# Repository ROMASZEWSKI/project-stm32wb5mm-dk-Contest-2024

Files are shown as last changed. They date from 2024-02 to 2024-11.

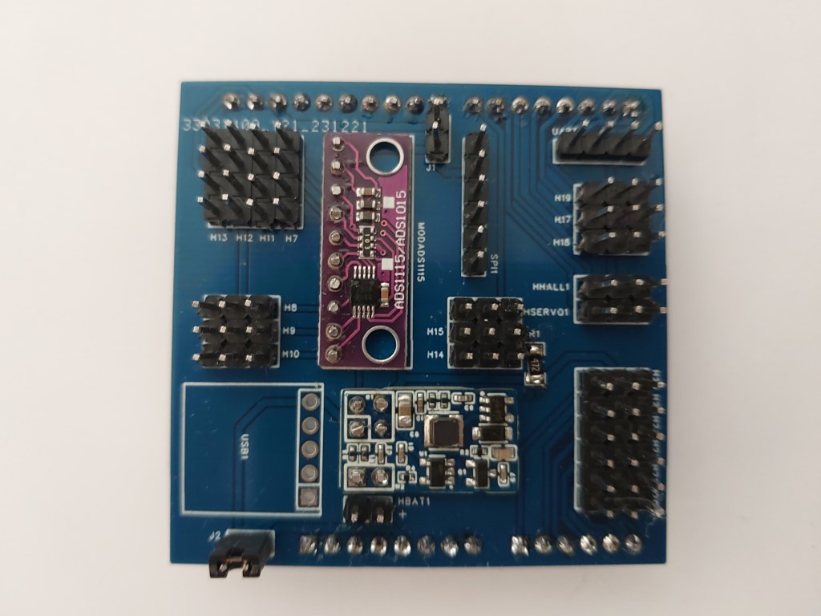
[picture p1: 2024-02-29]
photos/Assembled shield.jpg

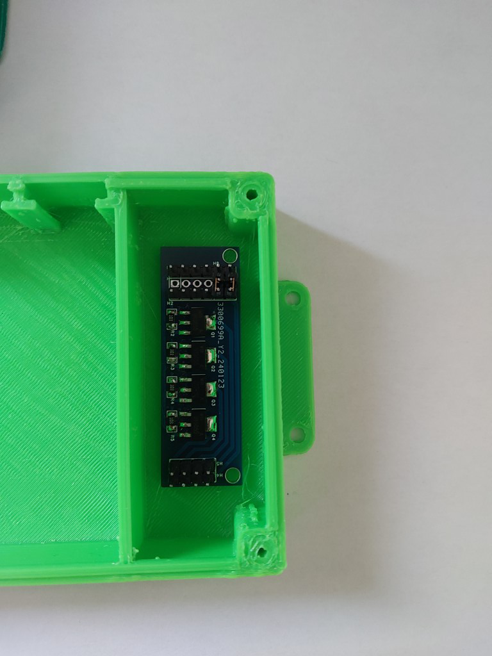
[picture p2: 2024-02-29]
photos/power module installation.jpg

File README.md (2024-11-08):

<h3>Zigbee Environmental measurement center for indoor plants or greenhouse</h3>

The goal of this project is to create with STM32WB5MM-DK a device allowing environmental measurements as well as monitoring of soil humidity and soil temperature of plantations with the management of an automation allowing automated watering and additional illumination according to the measurements.



<h3>Project description</h3>

Sensors in place (Petite)

The goal of this project is to create an environmental measurement unit, lighting and water supply for indoor plants or in a greenhouse using the stm32wb5mm-dk kit with communication in the Zigbee protocol to a server Mqtt linux on the internet through an Mqtt2Zigbee gateway under Windows 11, the information and automations then being processed by the Node-RED application under Linux with web user interface.
The persistence of data is performed by Node-RED to a MariaDB database under Linux.  
A box has been designed and printed on a 3D printer to accommodate the stm32wb5mm-dk card which will be fixed with 3 screws, the main diode is visible through the top case and a window is available to view the Oled display. The two buttons are mechanically transferred to the exterior. The two USB sockets are available and a way is provided for all the wiring. The sensors are fixed on the upper part, each with a receptacle and a window to the outside.

The device must carry out measurements of ambient temperature, ambient humidity, atmospheric pressure (BME280 component), Co2 level, air quality and volatile organic compound or TVOC level. (Ens160 component). An illumination sensor is present to measure the available light. Finally, a capacitive water level sensor is used and fixed to the low level of the water reserve.

Some measurements are taken at each plant using a capacitive sensor and a temperature probe (DS18B20 component). Capacitive sensors are measured with a 16-bit converter (ADS1115 component).

Most sensors can be used via the board's available I2C1 bus. One port is used to create a 1-wire bus for the 3 DS18B20s.

A switching board equipped with power MOSFETs is responsible for relaying the ports of the main board in order to manage 3 watering pumps and a relay for switching a special lamp for plants.

A switching power supply module provides complementary 3v3 power from the 5v source and powers the Shield. This card can also charge a battery and provide 3v3 if  5v is no more present.

The 3 pumps operating from 3v to 5v with brushless motors are immersed in the water reserve and a silicone hose supplies each plant.

In the event of lack of humidity in a plant, the planned automation takes care of supplying water with a given watering time until the desired humidity level is reached.

Phone SMS sending from node-RED is planned when the ambient or plant temperature is too high, when the air quality is too poor or when the water level is too low.

Datas are available and accessible via the Zigbee network, the card behaves as a server and as a router.

Datas are read and refreshed locally every 4s or fixed via an attribute .

The data can be viewed on the Oled display by selecting different screens using buttons 1 and 2.

To force the Zigbee pairing of the card at startup, button 1 must be pressed for 3 seconds.

The available and modifiable data for the lamp and the operating time of the pumps are available to be used by a Zigbee2mqtt coordinator, this coordinator is responsible for retrieving/modifying the information and retransmitting/monitoring topics (path to each data) on a mqtt server.

By using Node-RED specialized in retrieving and modifying Topics, it is possible with a graphical editor to display, storage in dataBase and make some automations.

This project uses different skills: digital electronics, printed circuit design, 3D printing creation, microcontroller programming, internet networks, Mqtt server, Node-RED server, Mariadb database, Linux system.

<h3>My goals are as follows:</h3>

- The first objective which constitutes this project is the commissioning of the stm32wb5mm-dk kit with the use of the sensors on the card and the use of additional sensors connected to a daughter card (two layers shield PCB) . The design of a two specific box printed in ABS or ASA, on 3D printer. The card works in Router/CLUSTER client-server mode. Interface to Zigbee2mqtt application and Node-RED interface.

- The second objective after is the creation of a printed card (4 layers) using the integrated component stm32wb55mmg with its shield (daughter card) and a power supply circuit with battery and solar panel, allowing the exploitation of the low power mode of the component .

Resumption of certain sensors from the first part.

Add water quality TDS sensor. Add high level sensor and automatic supply the water reserve.

- The third objective is to use and evaluate the Thread network in place of Zigbee.

<h3>Ressources links of the project</h3>

<h3>Project description </h3>
https://project.sophe.com/project_description.pdf<br/>
https://github.com/ROMASZEWSKI/project-stm32wb5mm-dk-Contest-2024/blob/main/project_description.pdf<br/>

<h3>All files of the project same as github</h3>
https://project.sophe.com/stm32ContestAllProject.zip
 
<b>For discovering the project :</b>
Read project_description.pdf<br/>
you find stm32cube_project.zip for stm32Cubeproject<br/>
https://github.com/ROMASZEWSKI/project-stm32wb5mm-dk-Contest-2024/blob/main/stm32cube_project.zip<br />
Parse PCB directory<br/>
https://github.com/ROMASZEWSKI/project-stm32wb5mm-dk-Contest-2024/tree/main/PCB<br/>
Parse 3D_print directory<br />
https://github.com/ROMASZEWSKI/project-stm32wb5mm-dk-Contest-2024/tree/main/3D_print<br/>
Parse zigbee2mqtt directory, you can read Zigbee2Mqtt_on_Windows_install.pdf <br />
https://github.com/ROMASZEWSKI/project-stm32wb5mm-dk-Contest-2024/tree/main/zigbee2mqtt<br/>
Parse node-RED directory, you can read Installation_of_node-RED and persistence.pdf <br />
https://github.com/ROMASZEWSKI/project-stm32wb5mm-dk-Contest-2024/tree/main/nodered<br />
And some photos and datasheets.<br />
https://github.com/ROMASZEWSKI/project-stm32wb5mm-dk-Contest-2024/tree/main/photos<br/>
https://github.com/ROMASZEWSKI/project-stm32wb5mm-dk-Contest-2024/blob/main/datasheets.zip<br>
<h3>New version updated with stm32CubeMX support and firmware 1.20 - November 2024</h3>
https://github.com/ROMASZEWSKI/project-stm32wb5mm-dk-Contest-2024/blob/main/greenhouse2.zip<br />

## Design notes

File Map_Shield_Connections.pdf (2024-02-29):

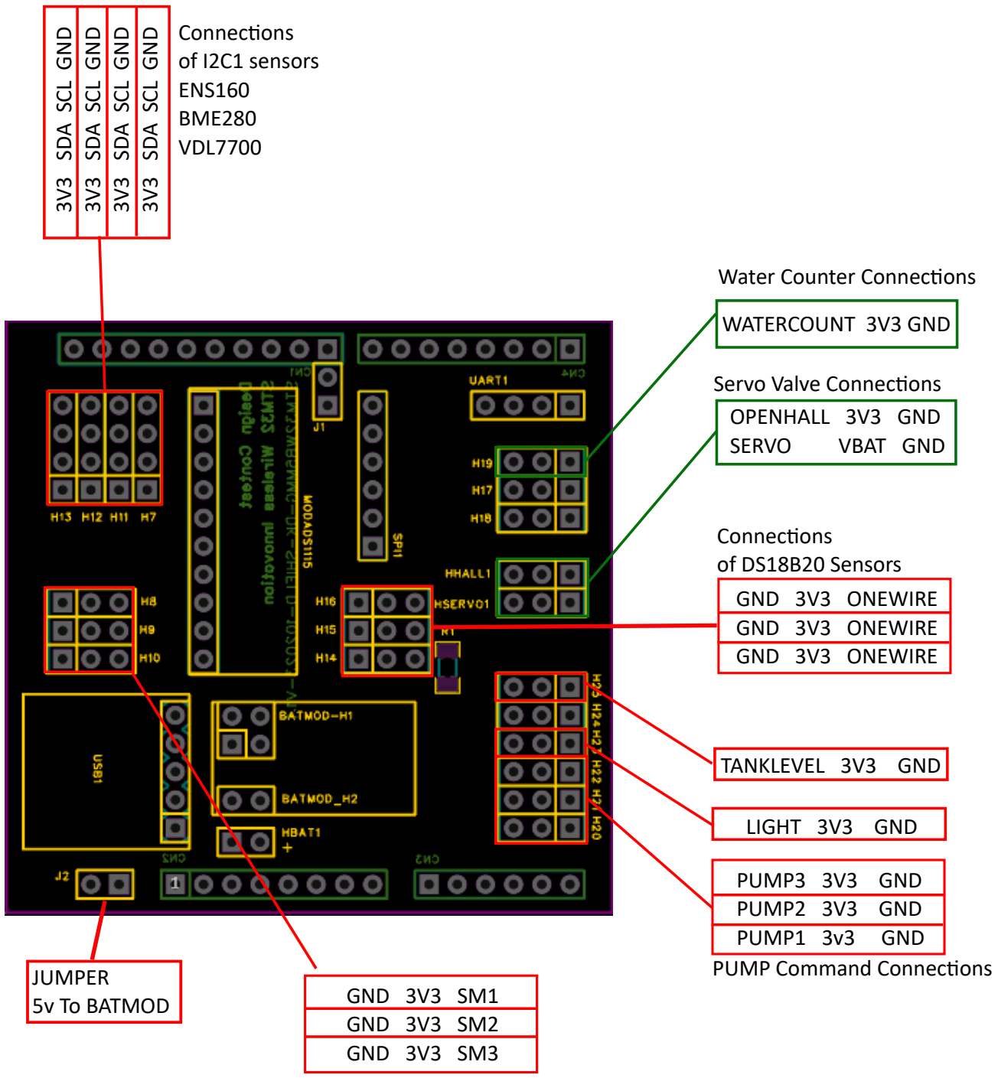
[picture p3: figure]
GND 3V3 ONEWIRE GND 3V3 ONEWIRE GND 3V3 ONEWIRE; JUMPER 5v To BATMOD; Connecons of I2C1 sensors ENS160 BME280 VDL7700; Connecons of DS18B20 Sensors; Water Counter Connecons; Servo Valve Connecons; PUMP Command Connecons; GND 3V3 SM1 GND 3V3 SM2 GND 3V3 SM3; 3V3 SDA SCL GND; PUMP3 3V3 GND PUMP2 3V3 GND PUMP1 3v3 GND; OPENHALL 3V3 GND; SERVO; VBAT GND; WATERCOUNT 3V3 GND; LIGHT 3V3 GND; TANKLEVEL 3V3 GND

Connecons
of Soil Moisture Sensors

Current project

## SHIELD CARD FOR STM32WB5MM-DK MODULE

Extended project

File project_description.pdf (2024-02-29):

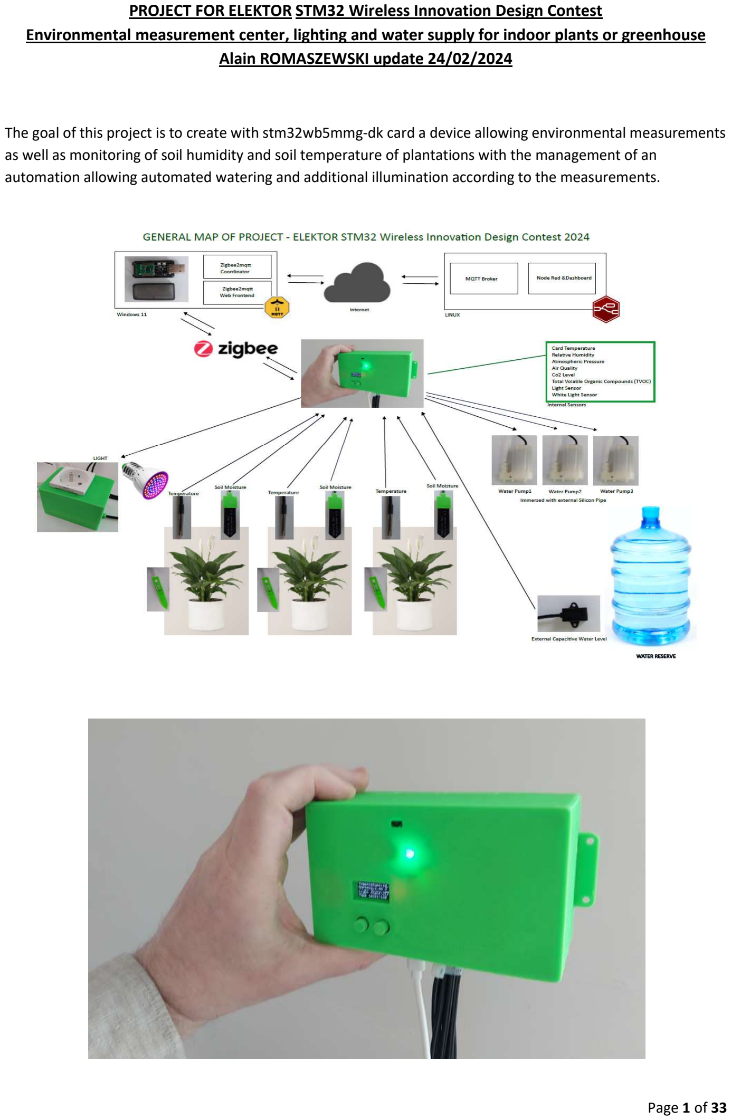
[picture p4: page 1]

Page 1 of 33

PROJECT FOR ELEKTOR STM32 Wireless Innovation Design Contest Environmental measurement center, lighting and water supply for indoor plants or greenhouse Alain ROMASZEWSKI update 24/02/2024

The goal of this project is to create with stm32wb5mmg-dk card a device allowing environmental measurements as well as monitoring of soil humidity and soil temperature of plantations with the management of an automation allowing automated watering and additional illumination according to the measurements.

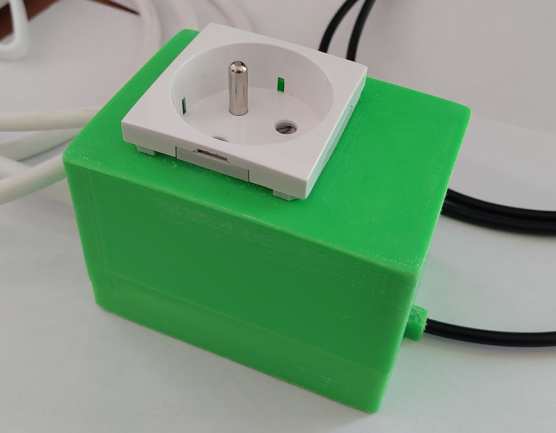
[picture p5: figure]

Page 2 of 33

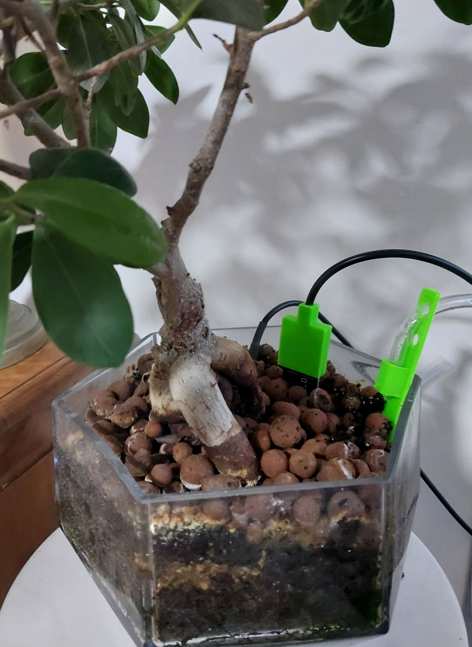
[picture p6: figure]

Project description

The objective of this project is to create an environmental measurement unit, lighting and water supply for indoor plants or in a greenhouse using the stm32wb5mm-dk kit with communication in the Zigbee protocol to a server Mqtt linux on the internet through an Mqtt2Zigbee gateway under Windows 11, the information and automations then being processed by the Node-RED application under Linux with web user interface.
The persistence of data is performed by Node-RED to a MariaDB database under Linux.

A box has been designed and printed on a 3D printer to accommodate the stm32wb5mm-dk card which will be fixed with 3 screws, the main diode is visible through the top case and a window is available to view the Oled display. The two buttons are mechanically transferred to the exterior. The two USB sockets are available and a way is provided for all the wiring. The sensors are fixed on the upper part, each with a receptacle and a window to the outside.

The device must carry out measurements of ambient temperature, ambient humidity, atmospheric pressure (BME280 component), Co2 level, air quality and volatile organic compound or TVOC level. (Ens160 component). An illumination sensor is present to measure the available light. Finally, a capacitive water level sensor is used and fixed to the low level of the water reserve.

Some measurements are taken at each plant using a capacitive sensor and a temperature probe (DS18B20 component). Capacitive sensors are measured with a 16-bit converter (ADS1115 component).

Most sensors can be used via the board's available I2C1 bus. One port is used to create a 1-wire bus for the 3 DS18B20s.

A switching board equipped with power MOSFETs is responsible for relaying the ports of the main board in order to manage 3 watering pumps and an external static relay for switching a special lamp for plants.

Page 3 of 33

A switching power supply module provides complementary 3v3 power from the 5v source and powers the Shield. This card can also charge a battery and provide 3v3 if 5v is no more present.

The 3 pumps operating from 3v to 5v with brushless motors are immersed in the water reserve and a silicone hose supplies each plant.

In the event of lack of humidity in a plant, the planned automation takes care of supplying water with a given watering time until the desired humidity level is reached.

Phone SMS sending from node-RED is planned when the ambient or plant temperature is too high, when the air quality is too poor or when the water level is too low.

Datas are available and accessible via the Zigbee network, the card behaves as a server and as a router.

Datas are read and refreshed locally every 500ms.

The data can be viewed on the Oled display by selecting different screens using buttons 1 and 2.

To force the Zigbee pairing of the card at startup, button 1 must be pressed for 3 seconds.

The available and modifiable data for the lamp and the operating time of the pumps are available to be used by a Zigbee2mqtt coordinator, this coordinator is responsible for retrieving/modifying the information and retransmitting/monitoring topics (path to each data) on a mqtt server.

By using Node-RED specialized in retrieving and modifying Topics, it is possible with a graphical editor to display, storage in dataBase and make some automations.

This project uses different skills: digital electronics, printed circuit design, 3D printing creation, microcontroller programming, internet networks, Mqtt server, Node-RED server, Mariadb database, Linux system.

My objectives are as follows:

- The first objective which constitutes this project is the commissioning of the stm32wb5mm-dk kit with the use of the sensors on the card and the use of additional sensors connected to a daughter card (shield) made on both sides. The design of a specific box printed in ABS or ASA, on a 3D printer. The card works in Router/CLUSTER client-server mode. Interface to Zigbee2mqtt, Node-RED interface.
- The second objective is the creation of a printed card (4 layers) using the integrated component
stm32wb55mmg with its shield (daughter card) and a power supply circuit with battery and solar panel, allowing the exploitation of the low power mode of the component .

Resumption of certain sensors from the first part.

Add water quality TDS sensor. Add high level sensor and automatic supply of the water reserve.

- The third objective is to use and evaluate the Thread network in place of Zigbee.

Project Hardware

Motherboard: stm32wb5mm-dk.

Page 4 of 33

This card consists of an integrated stm32wb55mmg component equipped with an M4 processor for processing and an M0+ coprocessor for BLUETOOTH, Zigbee and Thread communications.

We will deal here with Zigbee 3.0 mode. The card includes a OLED display of 128x64 pixels, 1 RGB diode, 2 push buttons, 1 sensitive key, 1 temperature sensor, 1 Gyroscopic and velocity sensor, 1 distance sensor, movements and a microphone.

The display is connected to the SPI interface and the sensors to the I2C3 bus. The card exposes different ports, an I2C1 bus, a Low Power UART and SPI bus among others.

Modules and sensors already present and used on the main card:

An OLED display for messages and displays.
A diode for signaling measurements taken.
First button to associate the server with the Zigbee coordinator when booting the system.
An STS22H temperature sensor integrated into the card (allowing you to know the temperature of the case and the card)
A gyroscope and velocity sensor (not necessarily useful here but exposed if necessary)
Two buttons used to scroll through the different displays. The same button can be used when booting the card to associate it with the Zigbee network.

Modules and sensors present on Shield card with Arduino type connectors:

A 16-bit (4-channel) ADS1115 type converter module. Allowing the measurement of battery voltage, the measurement of 3 soil humidity sensors.

Page 5 of 33

A BME280 type temperature, humidity and atmospheric pressure measurement module.

An ENS160 pollution and air quality measurement module, QA, Tvoc, Co2 measurement associated with an Aht25 sensor measuring temperature and hygrometry for the calibration of the ENS160 module.

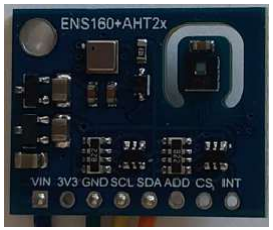
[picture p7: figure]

A VEML7700 type brightness measurement module.

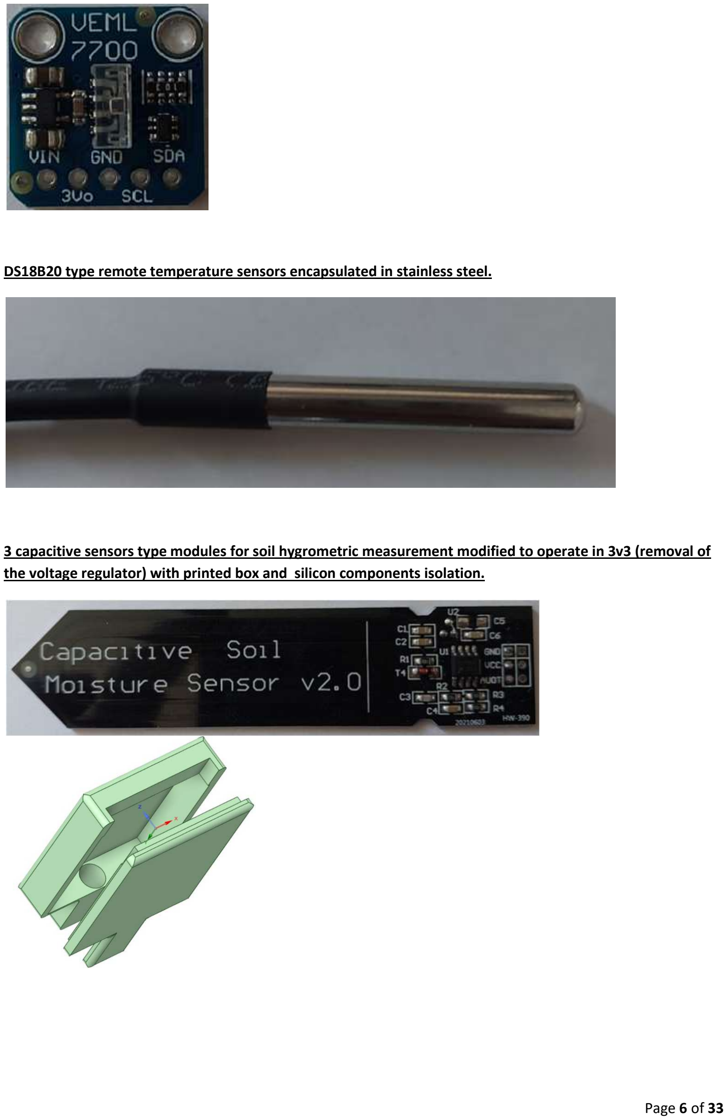
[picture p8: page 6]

DS18B20 type remote temperature sensors encapsulate

### 3 capacitive sensors type modules for soil hygrometric measurement modif

the voltage regulator) with printed box and

d in stainless steel.

type modules for soil hygrometric measurement modified to operate in 3v3 (removal of silicon components isolation.

Page 6 of 33

ied to operate in 3v3 (removal of

A power control module for activating 3 watering pumps. Eit activating Relay for Light.

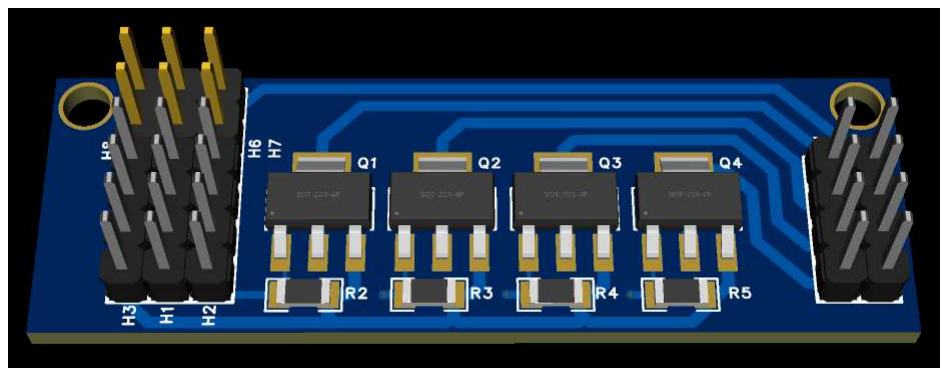
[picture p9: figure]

External box with Static Relay

her from 3v3/5v immersed

Page 7 of 33

brushless pumps and

Page 8 of 33

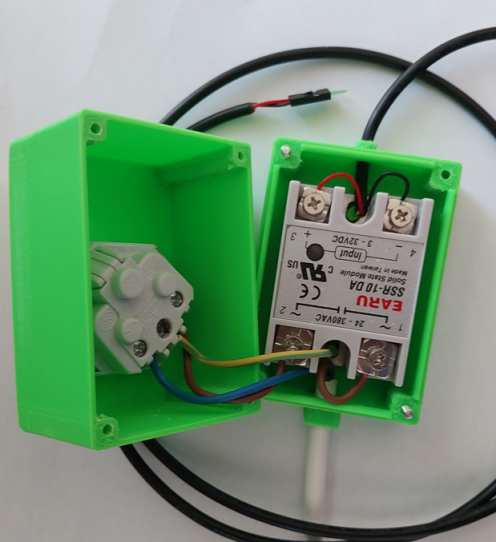
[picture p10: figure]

Schematic of connections in file joined.

Guide for pipe and pomp

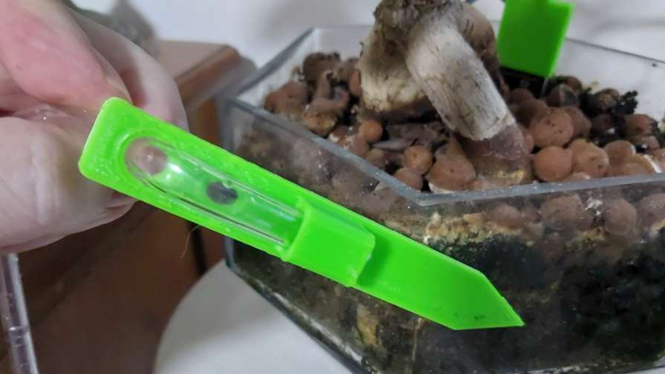
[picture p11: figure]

A capacitive module 3v3 detector for checking the low level of the water reserve.

Page 9 of 33

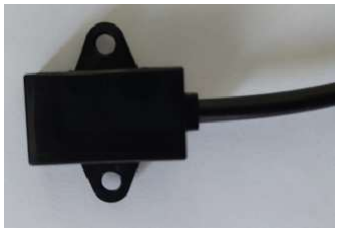
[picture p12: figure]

you need to attach the sensor using a double-sided adhesive to the lowest level of the tank.

A switching charging and power supply module to manage the charging of an 18650 battery used for pumps power and to provide up to 1A at 3.4 volts for the shield here, the input voltage is 5 volts

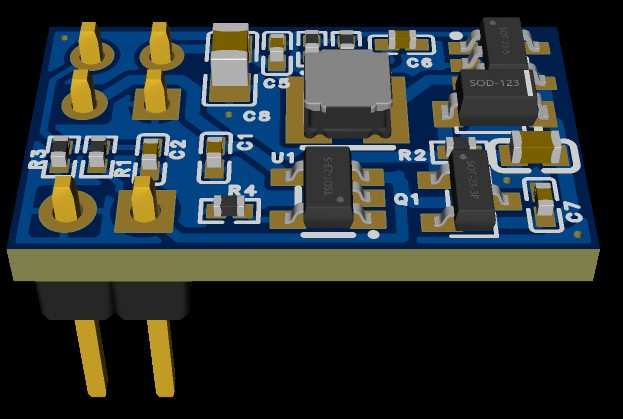
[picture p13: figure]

A shield card connected to the Arduino connectors on the stm32wb5mm-dk board.

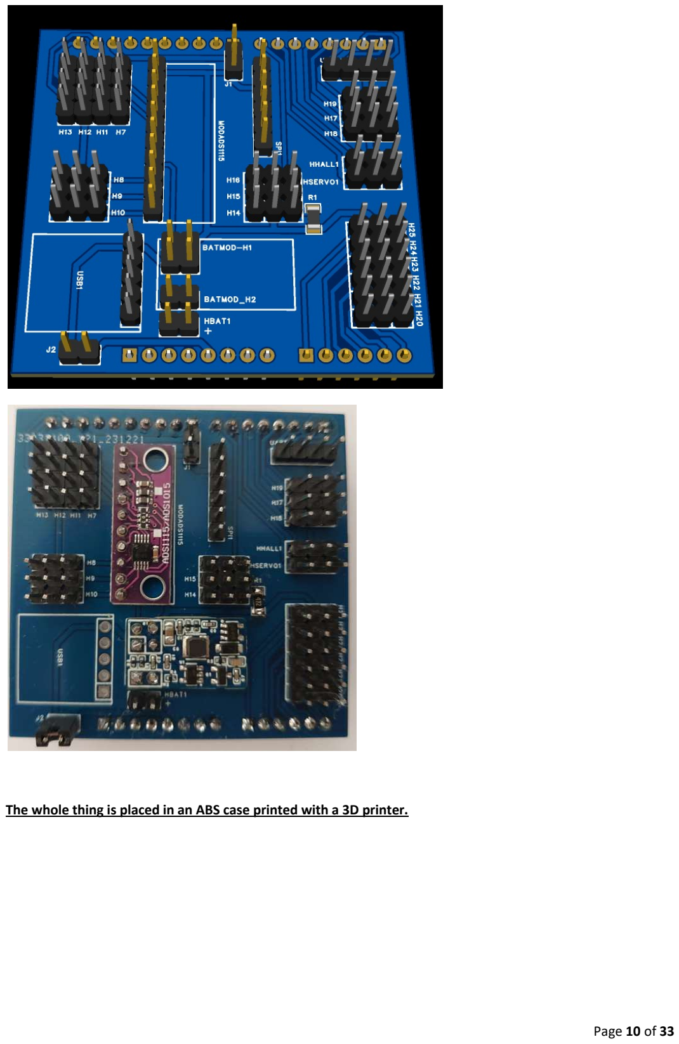
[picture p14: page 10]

Page 10 of 33

The whole thing is placed in an ABS case printed with a 3D printer.

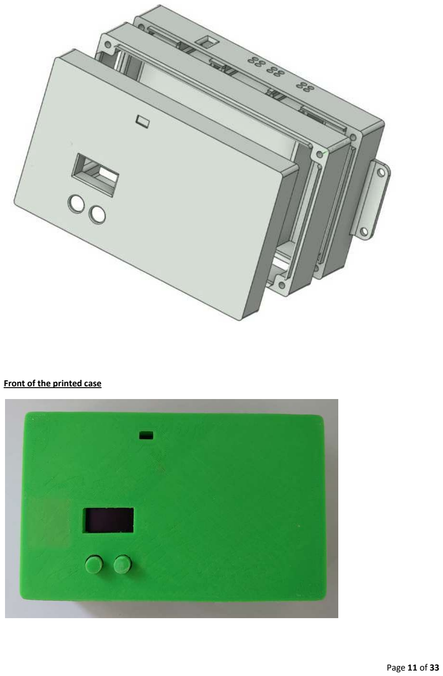
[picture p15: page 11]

Page 11 of 33

Front of the printed case

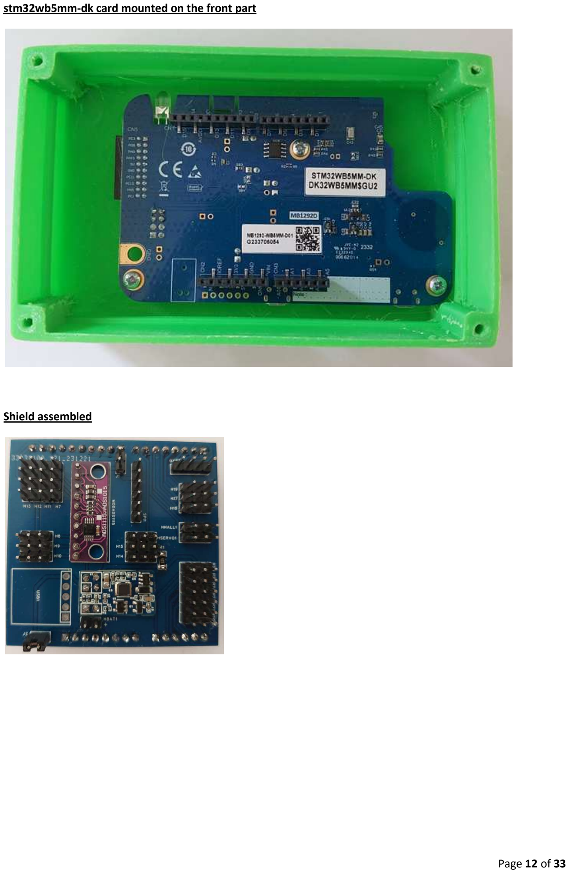
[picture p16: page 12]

Page 12 of 33

stm32wb5mm-dk card mounted on the front part

Shield assembled

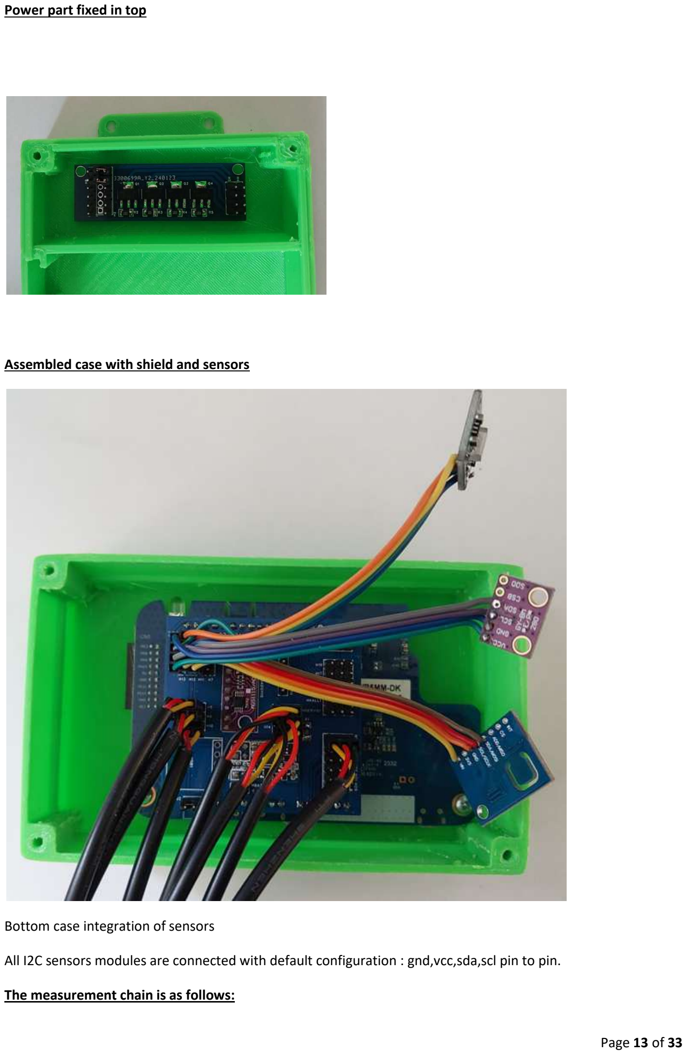
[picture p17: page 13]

Page 13 of 33

Power part fixed in top

Assembled case with shield and sensors

Bottom case integration of sensors

All I2C sensors modules are connected with default configuration : gnd,vcc,sda,scl pin to pin.

The measurement chain is as follows:

Page 14 of 33

The stm32wb5mmg-dk module and its daughter card exhibit regular measurements as a Zigbee server/router.

The zigbee2mqtt gateway client installed on a Windows 11 machine with a compatible Zigbee USB key is responsible for powering an MQTT event server installed on a remote server via the Internet. The gateway informs about the state of the network and the state of the attributes of the modules that have been associated with this gateway.

The results requested from the sensors are organized in a tree of Topics (access paths) on the MQTT server. MQTT GET requests are used to query the clusters of measurement results present on the remote Zigbee server.

It is also possible to transmit MQTT requests to modify a state or a value commanding an action to the Zigbee Remote client in order to activate, for example, a pump or a valve for a period of time.

Finally, the Node-RED application allows you to manage MQTT events and launch attribute readings from Clusters and launch actions via Mqtt set requests.

In passing, the events are stored in a MARIADB database to ensure the persistence of information and statistical processing of events.

Quick summary of the architecture of a Zigbee Network

The Zigbee protocol works using a mesh architecture and follows a communication model based on the master-slave principle. Here is an explanation of how the Zigbee protocol works:

Mesh Topology : Zigbee uses a mesh network topology, which means that each node (device or device) can communicate directly with other nodes nearby. Each node can act as a transmitter, a receiver and optionally a router.

Zigbee Nodes : There are three main types of Zigbee nodes:

1. Network coordinator (Zigbee Coordinator) : It is the main node which initializes and organizes the formation of the network.
2. Network router (Zigbee Router) : This node participates in the routing of information in order to facilitate its delivery. It can participate in the Zigbee network as End Nodes.
3. Zigbee End Devices : These are simple devices that join the Zigbee network. They are usually battery powered and are designed to minimize their power consumption.

Network Formation : When setting up a Zigbee network, the coordinator first emits a signal inviting other devices to join the network. Interested end nodes communicate with the coordinator to join the network. Once associated, endpoints can transmit data to this coordinator.

Master-Slave Communication: Zigbee uses a master-slave model, where the coordinator acts as the master of the network, and the end nodes are the slaves. End nodes can serve data to the coordinator, they cannot communicate directly with each other in most cases. However, using mesh topology, data can be routed through other nodes in the network to reach its destination with router node.

Security : Zigbee incorporates security mechanisms such as data encryption and device authentication.

Energy management : Zigbee is designed to be energy efficient, especially for battery-powered endpoints. Devices can go into sleep mode to save power and can be woken up when communication is needed.

Quick summary about the Zigbee protocol:

Page 15 of 33

Zigbee is based on the 802.15.4 physical protocol sharing the 2.4Ghertz WiFi frequency band. The band is divided into 16 channels (11 to 26), some channels are vacant and can be more particularly used in our case (15, 20, 25 for example). Of course all devices connected to the main coordinator must use the same channel as this one.

Each Router or Endpoint must first contact its coordinator in order to establish an exchange of keys and create a secure connection (or association). This session/association must be memorized between the Router/Endpoint and the coordinator.

This operation must be done once the network is installed, the coordinator authorizing this association only over a short period of time, each device having a unique 64-bit MAC address, the coordinator is also able to select and secure the association.

During the association, the coordinator retrieves a unique 64-bit address, allowing the Zigbee Node to be identified.

The Zigbee Node is divided into 1 or more EndPoints (between 1 and 240).

Each Endpoint has one or more Clusters representing a function standardized by the Zigbee or proprietary protocol with default attributes depending on the functions.

For each Cluster, it is therefore necessary to define its main function, its default and/or complementary attributes which can then be translated into a set of values or actions initiated by the coordinator.

Each attribute has a standardized 16-bit identifier, a value with a type (8, 16, 32, 64 bits, strings, enumeration, table, etc.). It can be read, written and/or reported on the network periodically or even persistent (its value is then memorized by the EndPoint). For Alarm or command mode the attribute can be transmitted to the coordinator as soon as the event occurs.

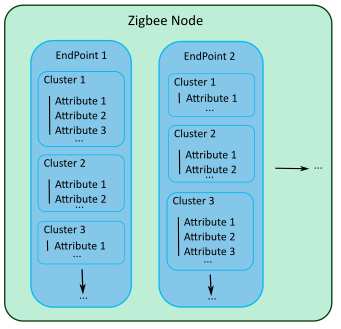
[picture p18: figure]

In our case of physical measurements to be taken, we will work as a query server on the attributes, the client coordinator being responsible for regularly querying the attributes in order to retrieve and store the information.

To carry out actions, the coordinator can modify attribute values on the EndPoint, the latter upon receipt will execute the requested tasks, indicating its state by modifying attributes.

Page 16 of 33

At the development level, ST Microelectronics has released a pre-compiled library for Cluster management. This is also accompanied by a Microcode intended for the M0+ communication coprocessor, depending on the final need and the desired protocol.

It is possible to add attributes to an existing Cluster depending on the desired final application.

Microcontroller Software Development Tool

For development, we will use the STM32CubeIDE v1.14.0 tool in C language, based on an existing Zigbee example.

It was necessary to rewrite drivers in C language available in the Arduino universe.

The existing example uses a non-preemptive pseudo system provided as an example by the manufacturer allowing the Zigbee network layer to be managed and tasks to be carried out sequentially by priority. https://www.st.com/en/development-tools/stm32cubeide.html

Zigbee2mqtt Gateway

This Open Source gateway works with the Node.js framework and is therefore programmed in Javascript. It can be installed under Linux or Windows environment.
It has a Web interface allowing you to manage the nodes and a configuration file allowing you to configure the gateway and recognize new nodes.

It can manage different Zigbee USB adapters on the market, here we will use a Zigbee 3.0 USB Dongle adapter based on Silicon Labs EFR32MG21 with pre-flashed EZSP V8.0.

It is responsible for transmitting the state of the gateway, the state of the nodes and the value of the node attributes to different Topics of an Mqtt server.

https://github.com/ROMASZEWSKI/zigbee2mqtt

https://github.com/ROMASZEWSKI/zigbee2mqtt-frontend

Managing MQTT data with Node-RED

This open source application works with the Node .js framework and is therefore programmed in Javascript. It can be installed under Linux or Windows environment.

It has a Web interface and allows you to process information flows from Mqtt servers, to work with databases (here MariaDB) and finally to generate events with scripts and graphic flows.

https://github.com/node-red/node-red

https://nodered.org/

Page 17 of 33

3D design

3D design is carried out by the free DesignSpark Mechanical 6 software (free version of SpaceClaim).

https://fr.rs-online.com/web/generalDisplay.html?id=designspark/designspark-mechanical

https://www.ansys.com/products/3d-design/ansys-spaceclaim

3D FDM printing

Printing is done with PrusaSlicer 2.6 software on an upgraded ANET ET 4 PRO.

The creations use either ABS filament or ASA filament (UV resistant).

https://www.prusa3d.com/en/page/prusaslicer_424/

https://anet3d.com/pages/et4

Printed Circuit Board Design

The design uses EasyEDA PRO v2.1.42 software and the ultra-fast, low-cost production line that goes with it.

https://easyeda.com/

Design and description of the functions of the shield card with Arduino connectors

This card has a soldered ADS1115 module (Fig.2) and a complementary soldered 5v -> 3.3v 1A switching power supply module with the possibility of battery charging so as not to overuse the power supply of the main map. The battery is not really useful at the moment but useful in subsequent projects.

It includes all the 2.54mm Dupont Male connectors for the various sensors.

Description of the main application

Installing or upgrade First the Firmware for M0+ Co-processor

the STM32WB5x processor works with an M0 co-processor which uses firmware provided by ST. This firmware is available in the STM32CubeWB PACK available here:

the stm32WB5x processor works with an M0 co-processor which uses firmware provided by ST. This firmware is available in the STM32CubeWB PACK available here:

https://github.com/STMicroelectronics/STM32CubeWB/tree/master/Projects/STM32WB_Copro_Wireless_Binaries/STM32WB5x

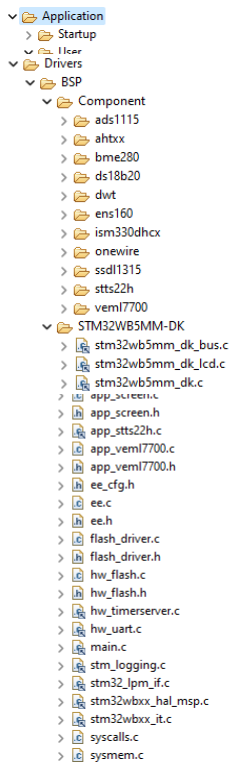
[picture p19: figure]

Page 18 of 33

We will use the stm32wb5x_Zigbee_FFD_fw.bin file in its revision 1.18.

Programming of the coprocessor is carried out via the FUS interface accessible via the STM32CubeProgrammer software.

Firmware file : stm32wb5x_Zigbee_FFD_fw.bin

Start Address : 0x080A0000

Description of the Drivers

In this directory we find the .c and .h drivers for the different sensors used:

ads1115: 16-bit AD Converter Driver.
ahtxx: Temperature and humidity sensor driver for calibration of the ENS160 bme280: Temperature, relative humidity and atmospheric pressure sensor driver.
ds18b20: Driver for 1-wire temperature sensors.
dwt: microsecond delay generator driver for onewire.
ens160: CO2, QA and Tvoc sensor driver. ism330dhcx: onewire gyroscope driver :
1-wire sensor driver
ssdl1315: Oled display driver
sts22h: temperature sensor driver of the
veml7700 card: light sensor driver.
The STM32WB5MM-DK directory which includes the button, RGB LED and Oled display drivers.

Application modules

app_ads1115: High level control of AD converter.

app_ahtxx: High level control of the temperature/humidity sensor of the ENS160
app_automat: Control of automations: Pumps, Light, level.

Page 19 of 33

app_bme280: High level control of the bme280 temperature/humidity/pressure sensor. app_clusters: definitions and activation of Zigbee clusters.

app_ds18b20: High level control of DS18B20 1-wire temperature sensors.
app_ens160: High level control of the pollution sensor: Co2, QA, TVoc.
app_entry: Groups the Zigbee protocol initialization subroutines.
app_ScheduleMeasure: Management of cyclical measurements and updating of Zigbee attributes and management of automations. Display of measurements by APP_DBG. MAIN PROGRAM
app_screen: Management of screens displaying the measurement results with selection by button 1 and 2 to scroll.
app_sts22h: High level control of the board temperature sensor.
app_veml7700: High level control of the light sensor.

ee, flash_driver,hw_flash: Set of subroutines used to emulate an eeprom on a Flash memory area of the processor. Used to save Zigbee connection information.
hw_timerserver: Management of timers for delays and the sequencer.

hw_uart: Serial interface management for APP_DBG displays.

main: Management of basic processor initialization.

stm_logging: management of debug displays to the serial link.

app_zigbee: this module configures the Zigbee layer, different calls are made to the modules described previously.

The application is based on the STM32_WPAN Middlewares library allowing the use of Zigbee communication.

Finally, the Utilities directory containing high-level management of the Oled display as well as sequencer for the management and synchronization of non-preemptive tasks.

Page 20 of 33

How the application works

The application configures on channel 15 Zigbee, an EndPoint 1 server, and a Temperature Measurement type cluster, proprietary attributes are then added to this standardized cluster. This choice was made after trying to create proprietary Cluster but after some trouble with the pre-compiled zcl library, on the other hand the application is stable and simple.

Cyclically, all sensors are interrogated and the results placed in each corresponding attribute of the Cluster, the delay is 20 seconds by default, but can be modified with a cluster attribute (ATTREFRESHMEAS).

The board's temperature sensor is used via the I2C3 interface.
The ADS1115, ENS160, BME280, VEML7700 and AHT25 sensors are used via the I2C1 interface. The soil humidity sensors have been modified to work at 3.3v and are connected to 3 inputs of the ADS1115 A/D converter. The first converter measures the Battery charging voltage.

The 3 DS18B20 1-wire bus type temperature sensors are connected to 1 PORT bit.
The Capacitive water tank level sensor is connected to 1 PORT bit.

The AHT25 temperature/humidity sensor supplied with the ENS160 must be interrogated less often because it tends to heat up, which is a shame for the measurement!

The activation of the pumps is managed by an activation time set in ms by their PlantWaterAlimentationX attribute (where X value is 1,2 or 3).

If this attribute is different from 0, the pump is started and the attribute is decremented by time to 0 and the pump is stopped. Each pump is on 1 PORT bit. The ON/OFF pump status is reported on a Cluster attribute PlantWaterAlimentationStateX.

If the Light attribute is 1 the light is on. 1 port bit. With the attribute PlantLight.

List of attributes

The app_clusters.h file lists the attributes used, each attribute has a 16-bit identifier.

Page 21 of 33

The app_clusters.c file declares the list of attributes to add to the Cluster.

Each attribute must be declared with its type, its minimum and maximum value, as well as its cyclical reportability or modification to the network.

The temperature in °C * 100 is a signed 16-bit integer.
The atmospheric pressure in hPa *10 is an unsigned 16-bit integer, not corrected with the altitude value. The relative humidity and soil humidity in % *10 is an unsigned 16-bit integer.
The battery voltage in mV is an unsigned 16-bit integer. The Co2 in ppm is an unsigned 16-bit integer. The Tvoc in pbm is an unsigned 16-bit integer.
The values in ohms of resistors R1, R2, R3 and R4 for gas detection are unsigned 32-bit integers.
The air quality is an unsigned 8-bit integer.
The motor and light on/off control is an unsigned 8-bit integer.
The water supply control is an unsigned 16-bit integer representing the time in ms.
The on/off pump state On/Off is an unsigned 8-bit integer.
The air quality sensor is an unsigned 8-bit integer.
The on/off tank level is an unsigned 8-bit integer.
The identifier DS18B20 is an unsigned 64-bit integer.

In order not to consume too much current on the card ports, a control module comprising 4 N-channel power MOSFETs makes it possible to control the pump motors and a relay for the lamp.

The app_automat.c file manages the automation and actions of the pumps, the lamp and the level sensor.

The app_SheduleMeasure.c file cyclically retrieves the value of the sensors by placing them in the Cluster attributes, a display is reported on the serial link.

The app_screen.c file manages the display of information screens, the different screens can be selected using the two buttons on the card for cyclical selection.

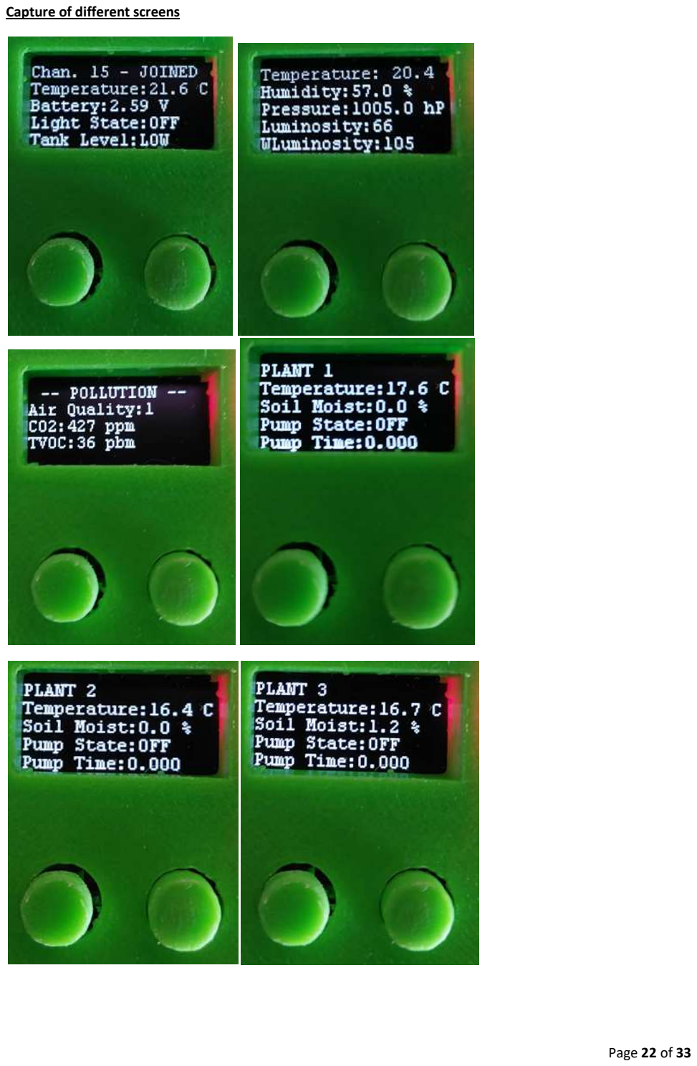
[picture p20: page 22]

Page 22 of 33

Capture of different screens

Page 23 of 33

Page 24 of 33

Installation and configuration of the Zigbee2Mqtt application

The Zigbee coordinator will be the Zigbee2Mqtt application installed on Windows 11 with a Zigbee 3.0 USB adapter based on Silicon Labs EFR32MG21 with EZSP v8.

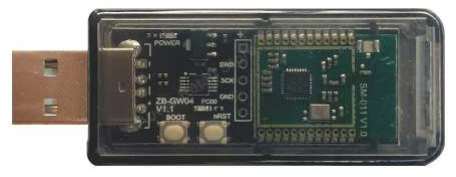
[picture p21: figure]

This application written in JavaScript with the Node.js framework will offer management of the coordinator via a Web interface and allow you to configure and transmit the state of each attribute of the Cluster to a Topic Set or Get of the remote Mqtt server. So by subscribing to an Mqtt Topic it is possible either to retrieve the value of the attribute or to modify it.

It will be necessary to modify the definition of Clusters in order to be able to correctly visualize the attributes.

You can discover this part in other documents and files join in zigbeetomqtt zip.

Installing an MQTT server

It is the MOSQUITTO application which will be used to manage an Mqtt server and will be installed on a Debian 12 VPS from OVH with ispconfig auto installation.

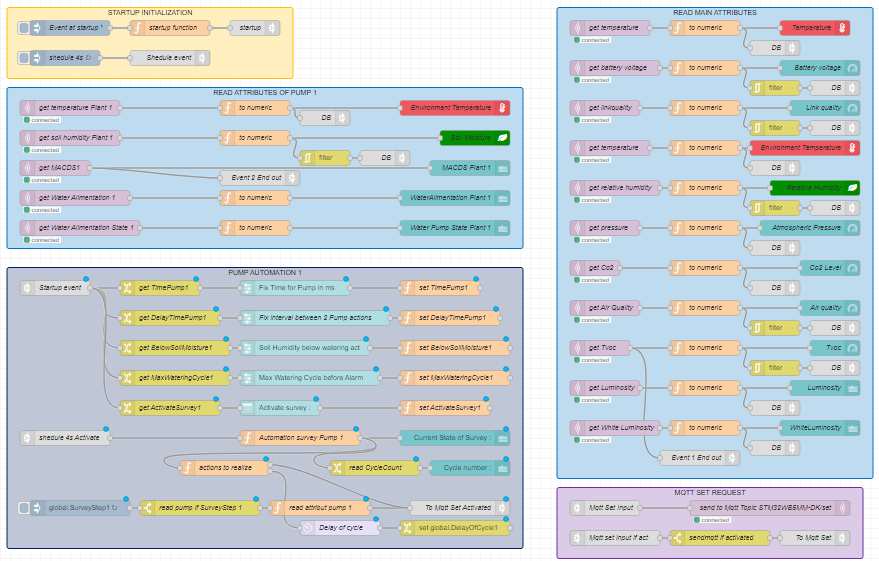
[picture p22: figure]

Page 25 of 33

Installation and configuration of the Node-RED application

This application written in Javascript and Node.js Framework allows you to connect to the Mqtt server and manage the storage of attributes in a database, as well as to carry out automation and alert management actions. It will be installed on a Debian 12 VPS.

This application has a web interface to graphically manage and schedule events. Another dashbord graphical interface allows you to view information and take action via widgets.

Node-RED have the capacity to request mqtt server and act with Mariadb database.

The flows of the project manage a light automation :

- Manual Light ON/OFF
- ON/OFF if brightness is too low.
- Sheduler with multiple times by week.
- Sheduler + brightness is too low.
- Solar Day/night + On if brightness is too low.

The flows of the project manage Pump automation :

- If the level of soil moisture is too low, it is possible to activate a cycle of watering with some limits and if

the water tank level is hight.(pumping delay and wait delay with a number of maximum cycle).

Screens of flows used :

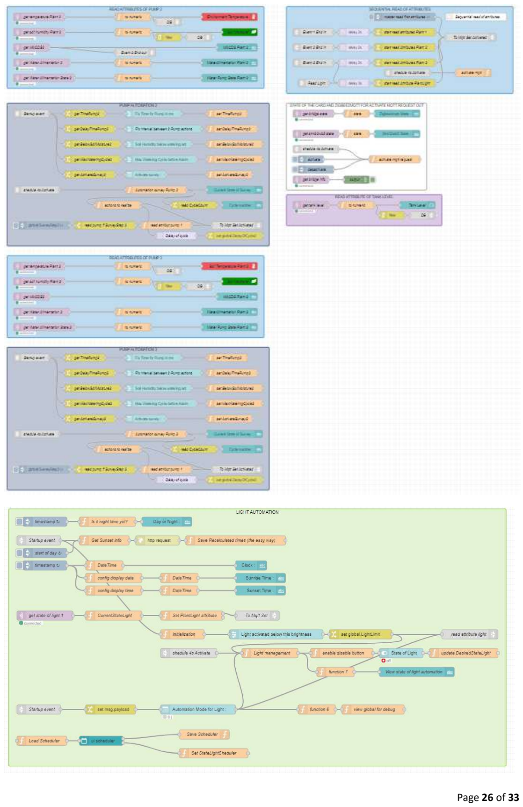
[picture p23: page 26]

Page 26 of 33

Page 27 of 33

All flows and detailed explanations are joined with this project in nodered directory.

NodeRed Dashboard sample screens

Page 28 of 33

Page 29 of 33

RESSOURCES LINKS OF THIS PROJECT

https://project.sophe.com/stm32ContestAllProject.zip

Page 30 of 33

Somes other details of my second goal in low power mode

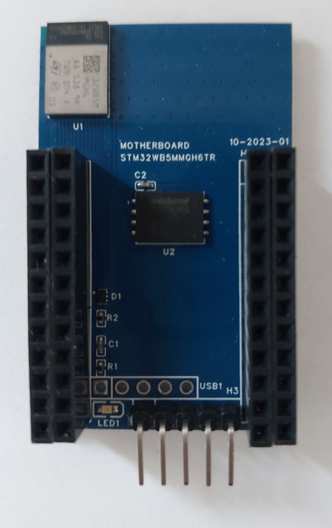
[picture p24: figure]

Creation of light motherboard (4 layers) with stm32wb5mmgh6tr and flash 32M for recording measure.

Very difficult to produce…

PCB attached to this project.

Programming with stm32programmer

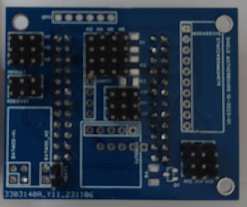
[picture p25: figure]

Shield for low power usage (2 layers)

PCB attached to this project

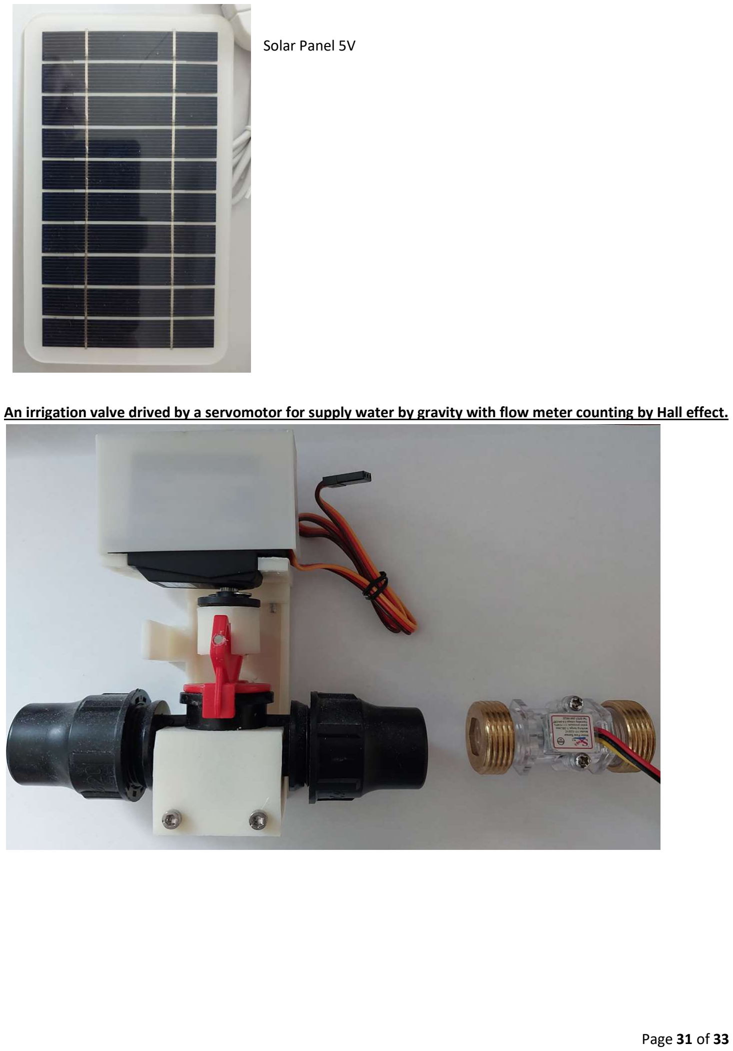
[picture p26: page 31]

Page 31 of 33

Solar Panel 5V

An irrigation valve drived by a servomotor for supply water by gravity with flow meter counting by Hall effect.


TDS Sensor for testing quality water

Integrate Zigbee2mqtt Coordinator and Mosquitto in

connected on ADS1115.

Page 32 of 33

Page 33 of 33

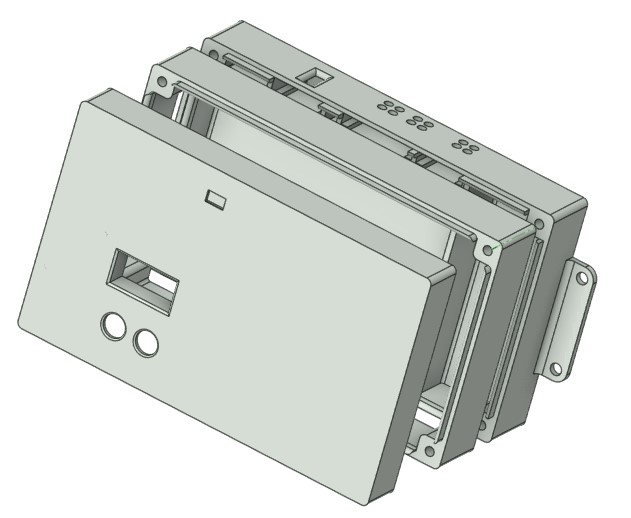
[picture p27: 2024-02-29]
photos/3D_design_from_top.jpg

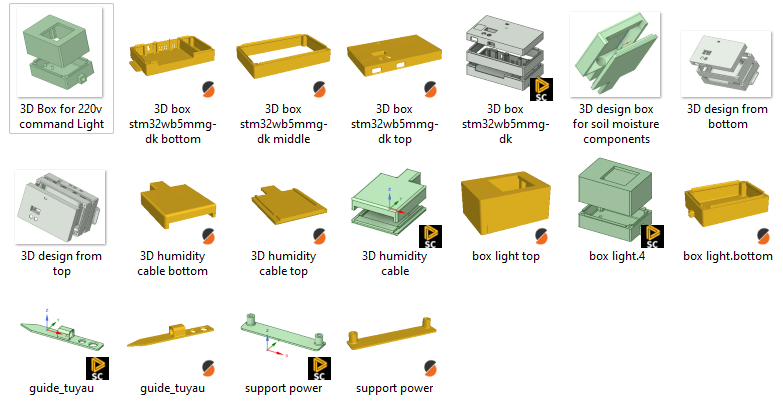
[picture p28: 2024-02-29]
photos/3D overview of models.png

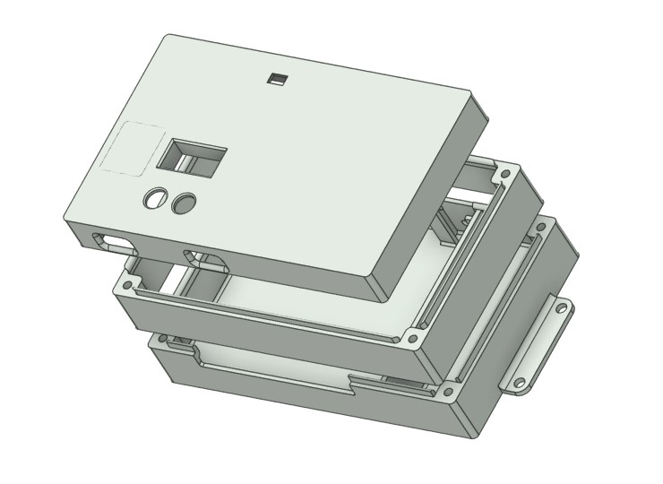
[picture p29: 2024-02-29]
3D_print/3D design from bottom.jpg

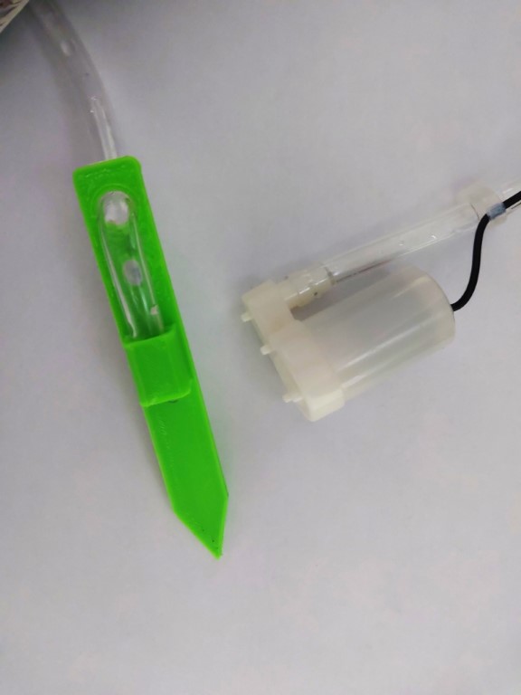
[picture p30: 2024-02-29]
photos/motor and pipe.jpg

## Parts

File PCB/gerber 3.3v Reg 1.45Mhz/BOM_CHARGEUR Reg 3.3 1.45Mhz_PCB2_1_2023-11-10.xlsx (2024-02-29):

No. | Quantity | Comment | Designator | Footprint | Value | Manufacturer Part | Manufacturer | Supplier Part | Supplier
1 | 1 | 1uF | C1 | C0402 | 1uF |  |  | C1525
2 | 3 | 100nF | C2,C5,C7 | C0402 | 100nF |  |  | C1525
3 | 1 | 10uF | C3 | C0603 | 10uF
4 | 1 | 8.2pF | C6 | C0402 | 8.2pF
5 | 1 | 10uF | C8 | C0805 | 10uF
6 | 1 | 1N5819W | D1 | SOD-123_L2.7-W1.6-LS3.7-RD |  | 1N5819W | Hottech(合科泰) | C2988774 | LCSC
7 | 1 | 2.2uH | L1 | IND-SMD_L3.0-W3.0 | 2.2uH | SWPA3015S2R2MT | Sunlord(顺络) | C43389 | LCSC
8 | 1 | CJ2301 | Q1 | SOT-23-3_L2.9-W1.3-P1.90-LS2.4-BR |  | CJ2301 | CJ(江苏长电/长晶) | C2910170 | LCSC
9 | 3 | 100K | R1,R2,R3 | R0402 | 100K
10 | 1 | 2K | R4 | R0402 | 2K
11 | 1 | 510K | R5 | R0402 | 510K
12 | 1 | 110K | R6 | R0402 | 110K
13 | 1 | TP4054 | U1 | TSOT-23-5_L2.9-W1.6-P0.95-LS2.8-BR |  | TP4054 | UMW(广东友台半导体) | C668215 | LCSC
14 | 1 | RT8059GJ5 | U2 | SOT-23-5_L3.0-W1.7-P0.95-LS2.8-BR |  | RT8059GJ5 | RICHTEK(立锜) | C20542 | LCSC

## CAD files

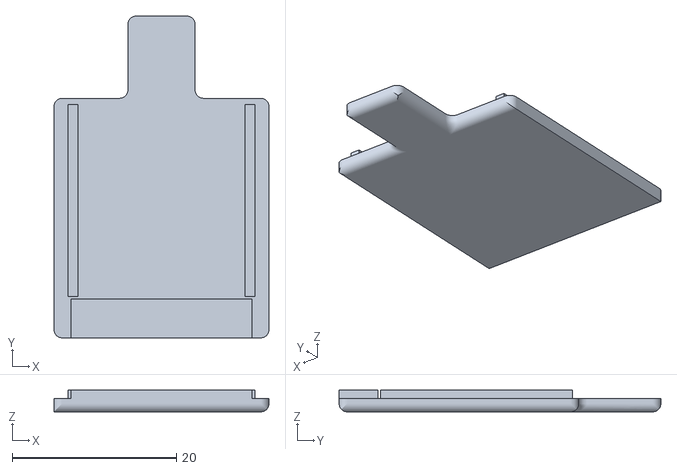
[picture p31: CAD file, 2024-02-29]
3D_print/3D humidity cable top.stl
26.2 x 39.2 x 2.65

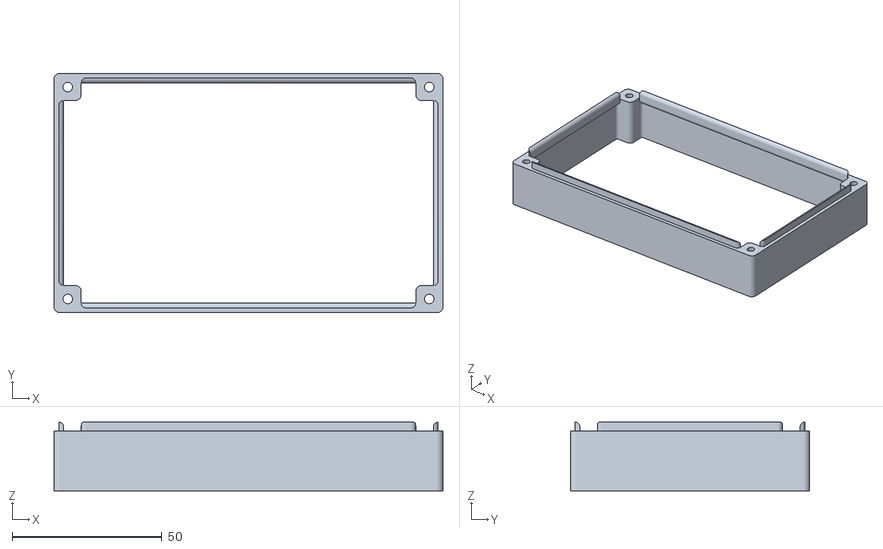
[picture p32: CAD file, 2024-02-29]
3D_print/3D box stm32wb5mmg-dk middle.stl
130.0 x 80.0 x 23.0

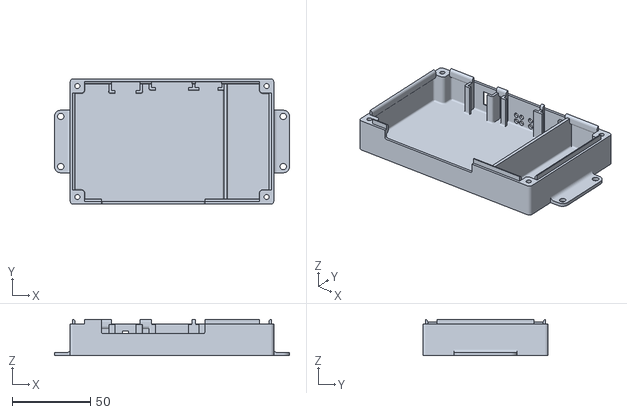
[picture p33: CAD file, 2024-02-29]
3D_print/3D box stm32wb5mmg-dk bottom.stl
150.0 x 80.0 x 23.0

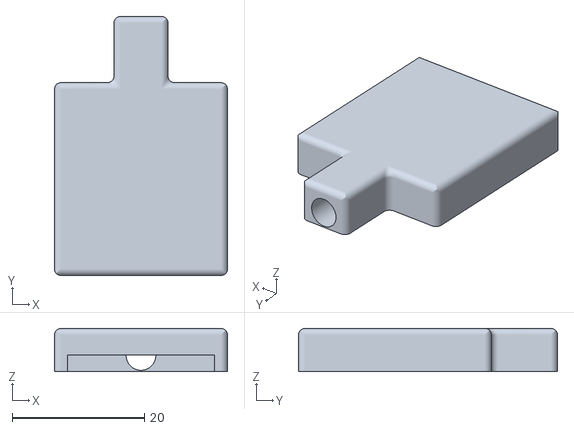
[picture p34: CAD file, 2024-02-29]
3D_print/3D humidity cable bottom.stl
26.2 x 39.2 x 6.55

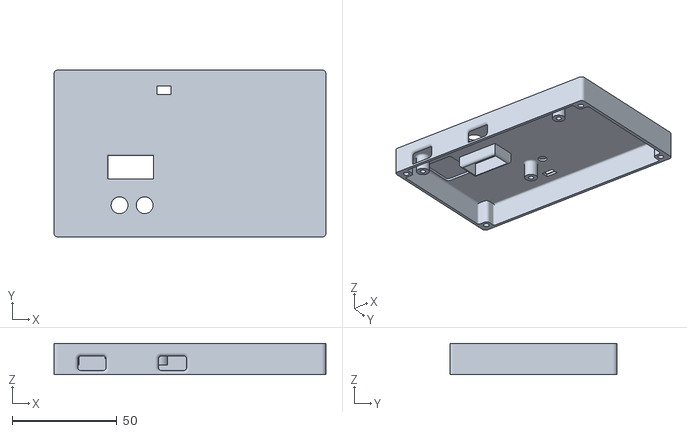
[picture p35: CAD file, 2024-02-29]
3D_print/3D box stm32wb5mmg-dk top.stl
130.0 x 80.0 x 15.0

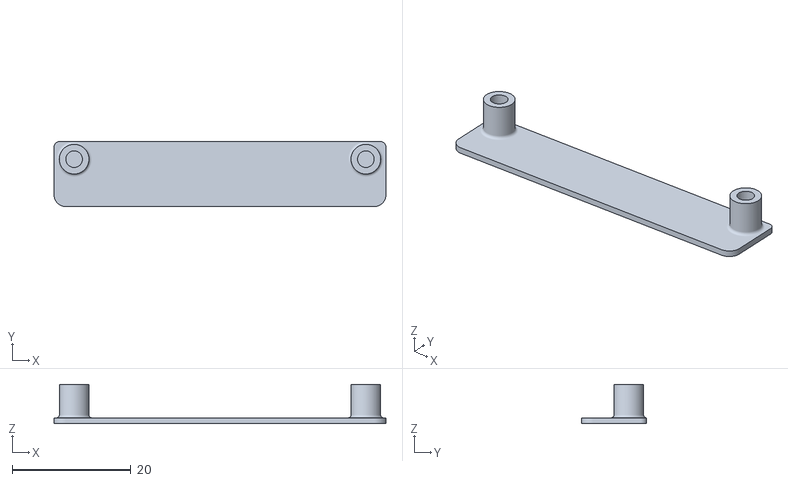
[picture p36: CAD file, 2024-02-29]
3D_print/support power.stl
56.0 x 11.0 x 6.65

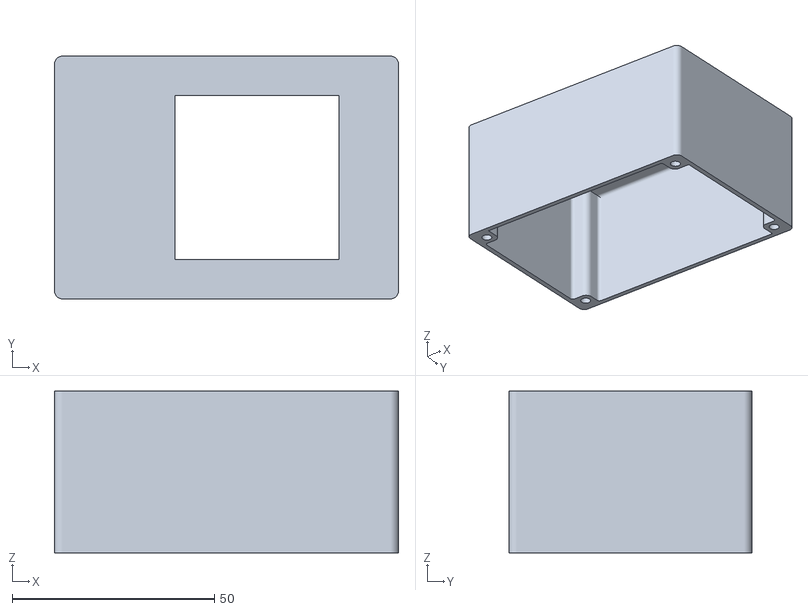
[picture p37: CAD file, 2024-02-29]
3D_print/box light top.stl
85.0 x 60.0 x 40.0

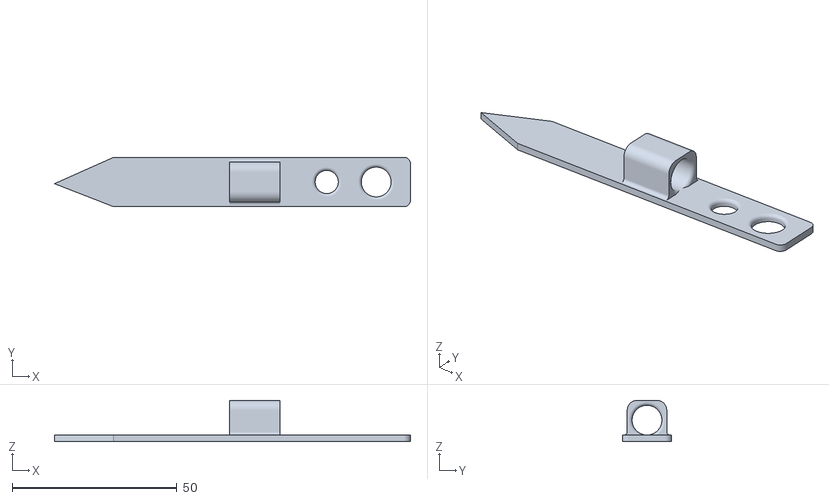
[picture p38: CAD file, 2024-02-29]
3D_print/guide_pipe.stl
108.0 x 15.0 x 12.5

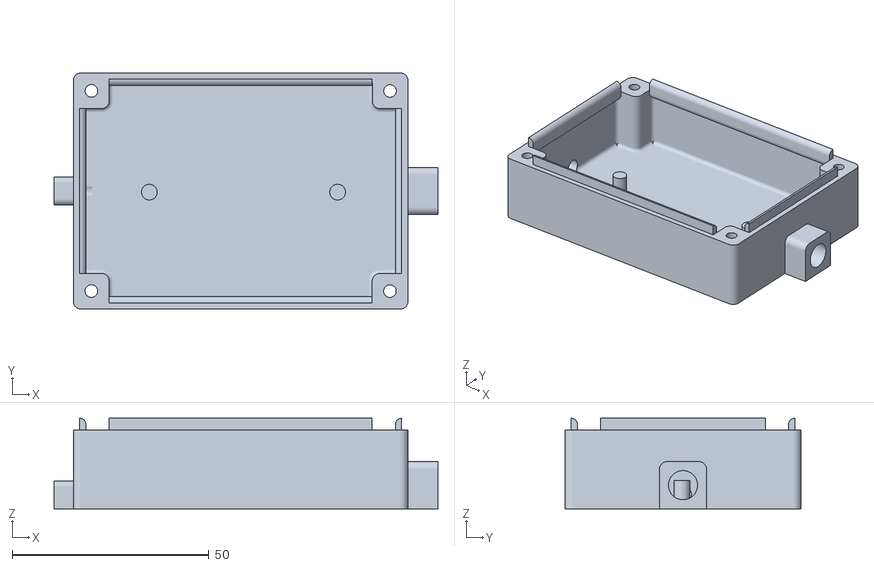
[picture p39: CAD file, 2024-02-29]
3D_print/box light.bottom.stl
97.5 x 60.0 x 23.0

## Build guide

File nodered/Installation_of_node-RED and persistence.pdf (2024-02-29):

Page 1 sur 17

## Node-RED installation and MariaDB persistence

Download & Install Node.js

Node.js is a library specialized in network and written in javascript.

For debian you must use this link : https://nodered.org/docs/getting-started/raspberrypi

It is good for raspberry and debian linux.

After you have access to nodeRED with http://<hostname>:1880.

For me i have a rewrite for access from a normal url.

In nodeRED you can add the plugins into the palette :

You must add these plug-ins to the project with manage palette>install :

1. @studiobox/node-red-contrib-ui-widget-humidity-tree
2. @studiobox/node-red-contrib-ui-widget-thermometer

### 3. node-red 3.1.3

### 4. node-red-contrib-config

### 5. node-red-contrib-ui-artless-gauge

### 6. node-red-contrib-ui-spinner

### 7. node-red-contrib-ui-time-scheduler

### 8. node-red-dashboard 3.6.2

### 9. node-red-node-mysql 2.0.0

### 10. node-red-node-ui-lineargauge 0.3.7

For saving globals variables of the project after each deploiement . You must modify your file settings.js in /<user nodered>/.node-red/settings.js and add

contextStorage: {
default: {
module:"localfilesystem"
},
},
You must restart with : service nodered restart

From the file

You have access to the imported flow :

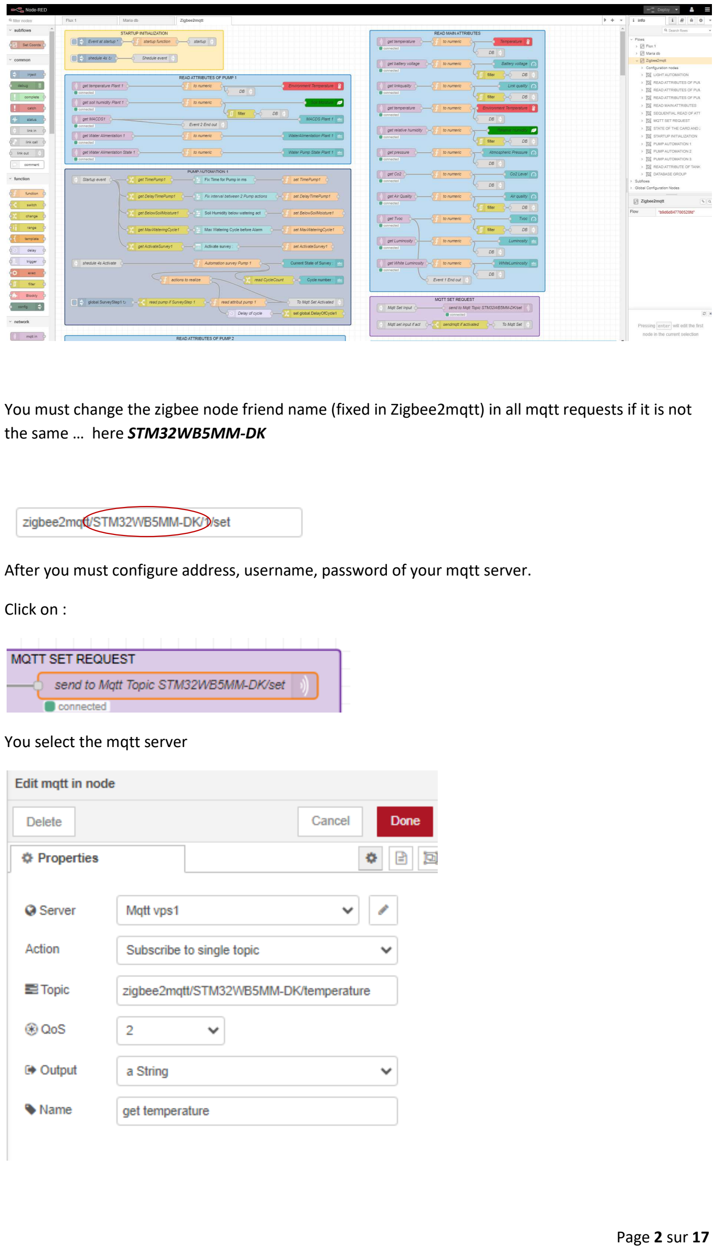
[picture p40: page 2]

Page 2 sur 17

You must change the zigbee node friend name (fixed in Zigbee2mqtt) in all mqtt requests if it is not

the same … here STM32WB5MM-DK

After you must configure address, username, password of your mqtt server.

Click on :

You select the mqtt server

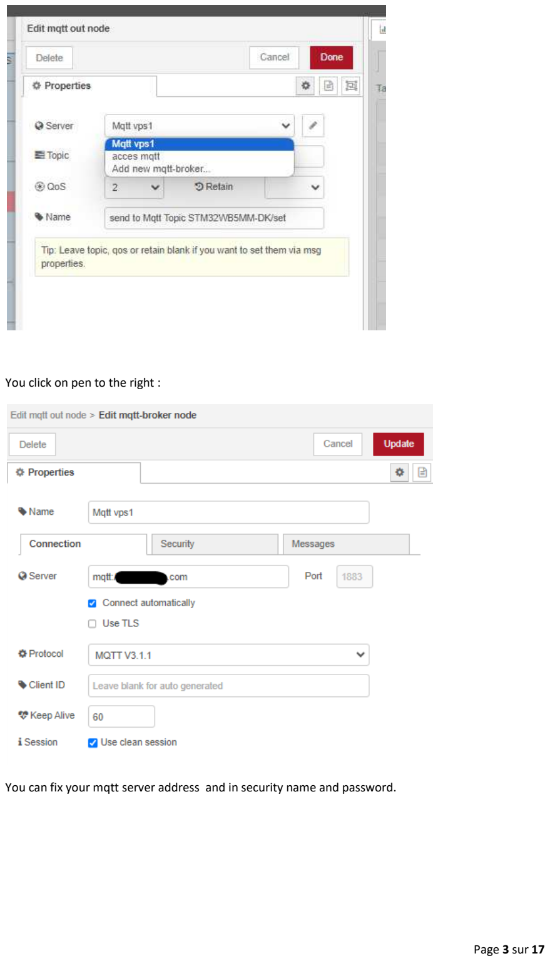
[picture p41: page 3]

Page 3 sur 17

You click on pen to the right :

You can fix your mqtt server address and in security name and password.

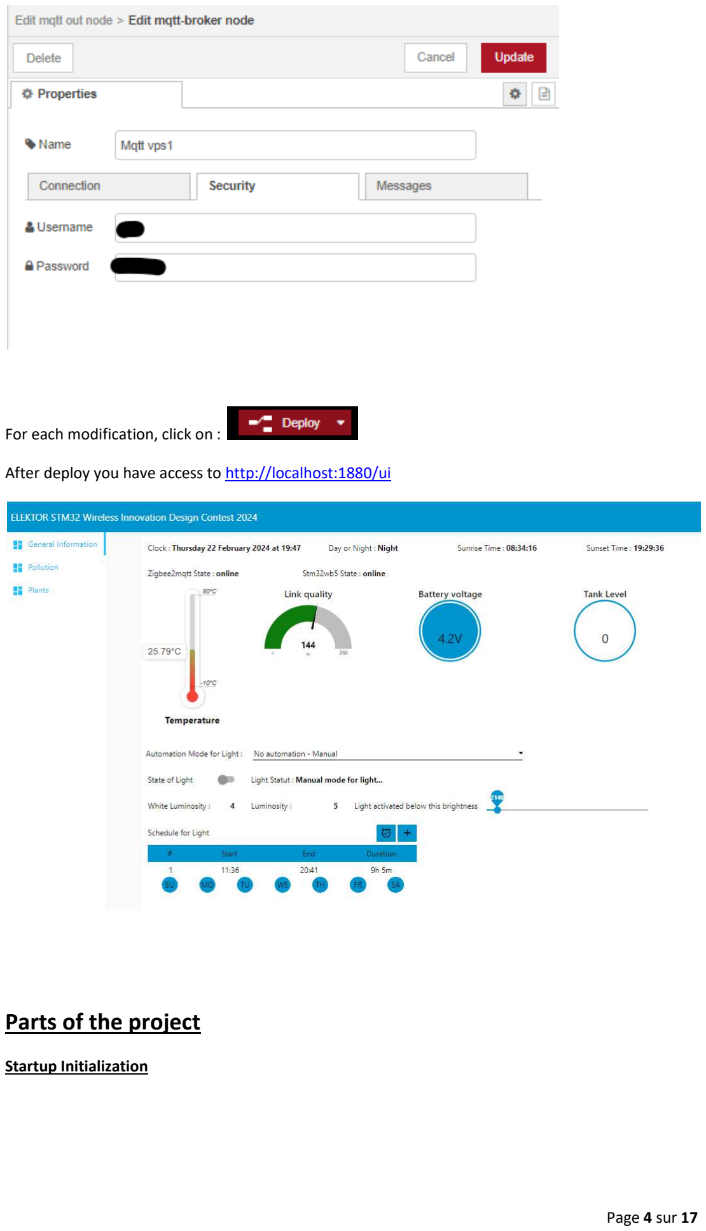
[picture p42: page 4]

Page 4 sur 17

For each modification, click on :

After deploy you have access to http://localhost:1880/ui

## Parts of the project

Startup Initialization

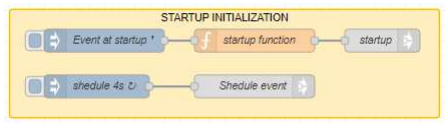
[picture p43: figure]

Page 5 sur 17

run one time at the begin.

run every 4 seconds for sheduling the different threads.

this function initialize all the globals variables and data for day and night of your place.

global.set("Latitude", 42.6887); global.set("Longitude", 2.8948); global.set("Tz",3600);
global.set("timezone","Europe/Paris"); global.set("language","en-GB");

anchor for send event at startup

anchor for send event every 4 seconds.

Read main Attributes

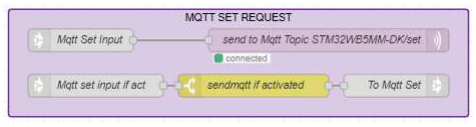
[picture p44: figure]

Page 6 sur 17

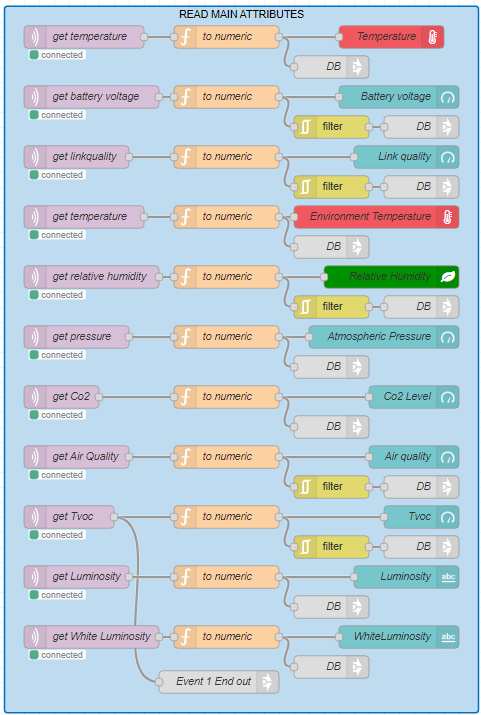
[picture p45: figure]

Each | of this type send an event when a new mqtt topic come.

The data are placed in global variable or/and to a graphical dashboard widget.

This event | start the read of next attributes for no stress of zigbee.

With stm32wb5 it is not possible to read more of 8 attributes at each request. (limitation ?)

MQTT SET REQUEST

this group allows you to transmit requests to read or write attributes. Two possibilities, directly or with verification of the presence of the stm32 card and active zigbee2mqtt.

SEQUENTIAL READ OF ATTRIBUTES

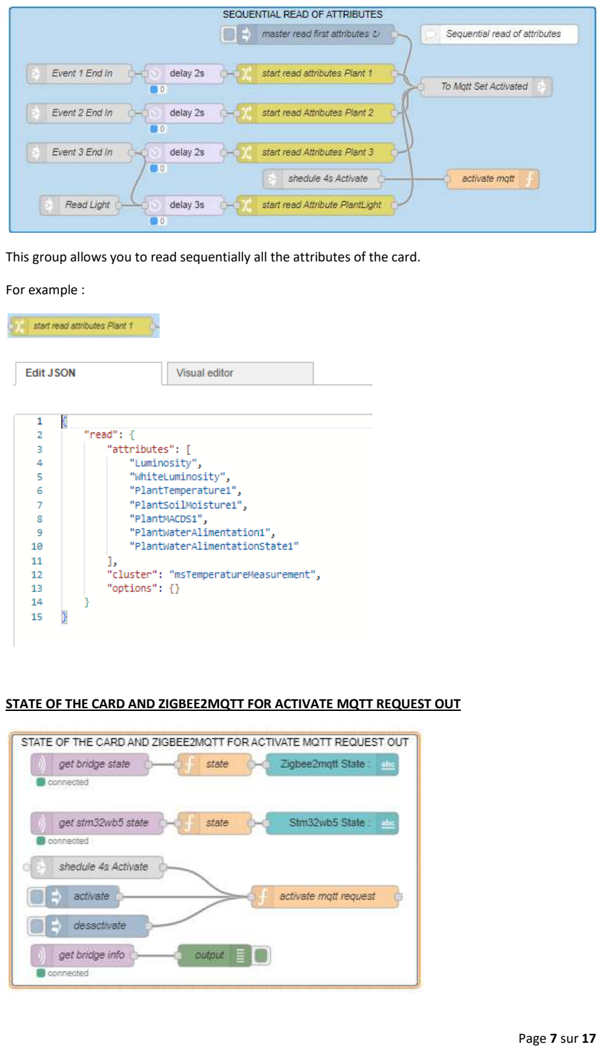
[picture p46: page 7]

Page 7 sur 17

This group allows you to read sequentially all the attributes of the card.

For example :

STATE OF THE CARD AND ZIGBEE2MQTT FOR ACTIVATE MQTT REQUEST OUT

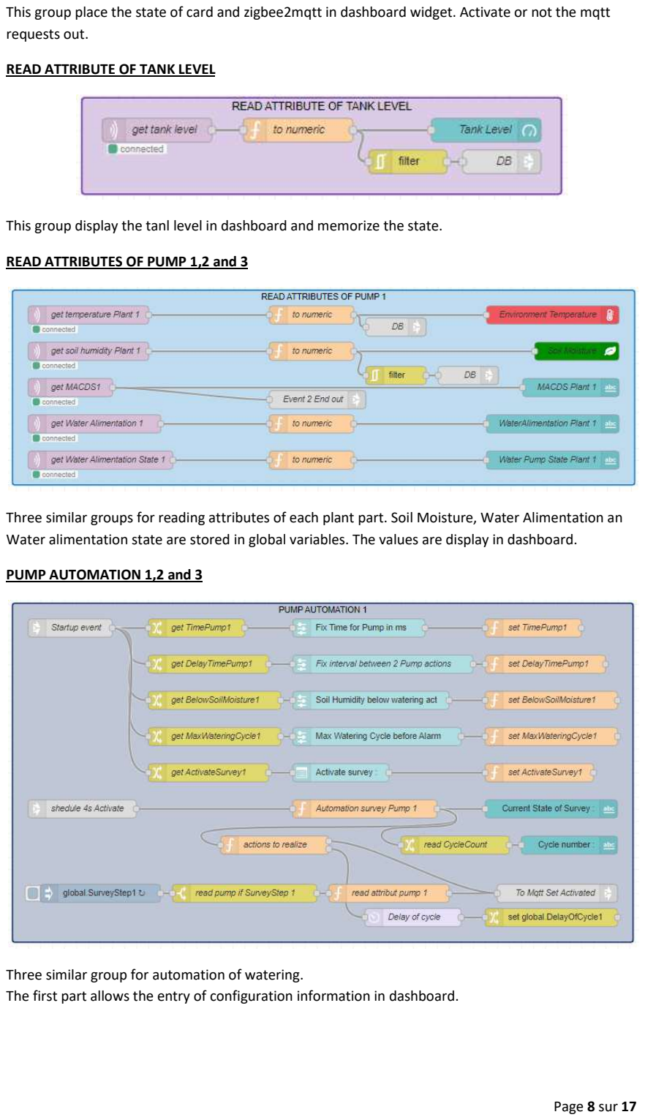
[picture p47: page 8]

Page 8 sur 17

This group place the state of card and zigbee2mqtt in dashboard widget. Activate or not the mqtt requests out.

READ ATTRIBUTE OF TANK LEVEL

This group display the tanl level in dashboard and memorize the state.

READ ATTRIBUTES OF PUMP 1,2 and 3

Three similar groups for reading attributes of each plant part. Soil Moisture, Water Alimentation an Water alimentation state are stored in global variables. The values are display in dashboard.

PUMP AUTOMATION 1,2 and 3

Three similar group for automation of watering.
The first part allows the entry of configuration information in dashboard.

Page 9 sur 17

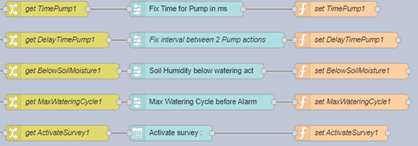
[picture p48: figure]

The logic is to initialize the widget with a global variable and store the new user value in this same variable.

The main function is :

msg.payload="";
msg.topic="";
msg.delay=0;
msg.wa="";
// verify if mqtt and stm32 board actives if (global.get("StateSendMqtt")==1)
{
switch(global.get("ActivateSurvey1")) {
// no survey
case 0:
global.set("SurveyStep1",0); global.set("CycleCount1",0);
msg.CycleCount = global.get("CycleCount1"); msg.topic = "No survey activity...";
break;
// Automation of survey
case 1:
if ( (global.get("TankLevel")==0) || (global.get("MaxWateringCycle1")==global.get("CycleCount1")) ) {
msg.topic = "Warning : Water tank level to Low !";
if (global.get("MaxWateringCycle1") == global.get("CycleCount1"))
msg.topic = "Warning : Watering stopped because Too many cycle !"; }
else
{
switch(global.get("SurveyStep1"))
{
// compare soil moisture and pass to step 1
case 0:
if (global.get("SoilMoisture1") < global.get("BelowSoilMoisture1")) {
// mqtt msg for setting action time of pump 1
msg.wa = {
"write":
{
"cluster": "msTemperatureMeasurement",
"options": {},
"payload": {
"PlantWaterAlimentation1": global.get("TimePump1") }
}
};

Page 10 sur 17

global.set("SurveyStep1",1); msg.topic = "Start pump..."; }
else
{
global.set("CycleCount1",0); msg.topic = "Survey Soil Moisture..."; }
break;
// wait for pump to 0 ms
case 1:
if (global.get("WaterAlimentation1")==0)
{
global.set("SurveyStep1",2);
msg.topic = "Start Delay for next Watering..."; msg.delay = global.get("DelayTimePump1")*60; global.set("DelayOfCycle1",0);
}
else
{
msg.topic = "Pump Running...";
}
break;
// wait for delay between watering act and return to 0 // increment step and alarm if problem

case 2:
if (global.get("DelayOfCycle1")==1)
{
global.set("SurveyStep1", 0);
global.set("CycleCount1", global.get("CycleCount1")+1); msg.topic = "Survey Soil Moisture...";
}
else
msg.topic = "Start Delay for next Watering..."; break;
}
}
break;
default:
break;

}
}
else
{
msg.topic = "Wait for Zigbee2mqtt or stm32 activity..."; }

return msg;

This program if a user activate the survey with the dropdown box.

Verify if the tank level is Hight and display a message if it is too low.

Manage 3 steps by loop:

Step 0 : verify if soil moisture below the fixed set point.

If no, stay in step 0

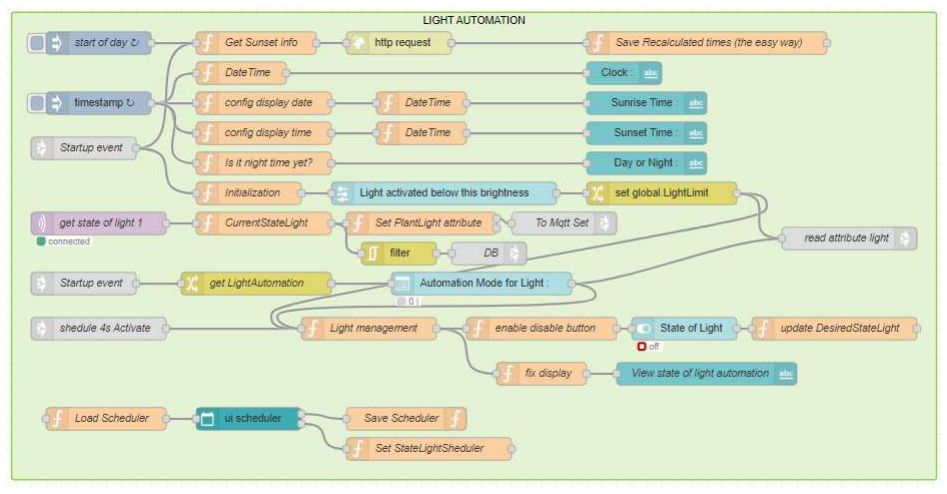
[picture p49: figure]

Page 11 sur 17

If yes start the pump with the time fixed by the user, after pass to step 1.

Step 1 : If WaterAlimentation attribute is 0, the pump is now stopped and a delay of wait start with fixed value in minutes. (time for soil moisture react).
Pass to step 2.

If water alimentation attribute is 1, display « pump is running »

Step 2 : Wait end of the delay. At the end increment the counter of loop and pass tostep 0 for a next loop

If the maximum of loop fixed arrived.

LIGHT AUTOMATION

This group manage the light automation.

The functionnalities with the dropdown box in dashboard :

- Activate manually the Light.
- Activate the Light when the Brightness is too low.
- Activate the Light with a Sheduler.
- Activate the Light with a Sheduler and when the Brightness is too low.
- Activate the Light with if the Brightness is too low and if it’s Day. (Sunrise and Sunset gets

from website every day with API http)

This first Part initialize the widgets, sunset,sunrise,day and night. Fix the state of light.

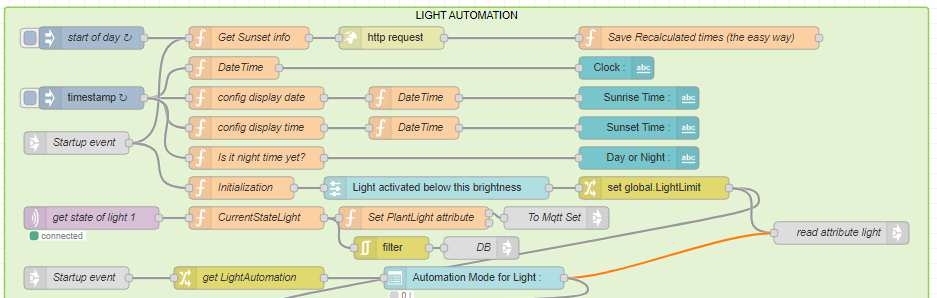
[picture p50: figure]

Page 12 sur 17

This part manage the automation

The program of

msg.payload="";

msg.topic="";

// verify if mqtt and stm32 board actives

if (global.get("StateSendMqtt")==1)

{

switch(global.get("LightAutomation"))

{

// manual

case 0:

msg.topic = "Manual mode for light...";

break;

// Light On if Luminosity to low

case 1:

if (global.get("LightLimit") > global.get("Luminosity")) {

msg.topic = "Light On because Brightness is low...";

global.set("DesiredStateLight",1);

}

else

{

msg.topic = "Light Off because Brightness is hight...";

global.set("DesiredStateLight", 0);

}

break;

// use sheduler for light on

case 2:

if (global.get("StateLightSheduler") == 1) {

msg.topic = "Light On by sheduler...";

global.set("DesiredStateLight", 1);

}

else {

Page 13 sur 17

msg.topic = "Light Off by sheduler...";

global.set("DesiredStateLight", 0);

}

break;

// use sheduler and level

case 3:

if (global.get("StateLightSheduler") == 1) {

if (global.get("LightLimit") > global.get("Luminosity")) {

msg.topic = "Light On by sheduler and Brightness is low...";

global.set("DesiredStateLight", 1);

}

else {

msg.topic = "Light Off by sheduler and Brightness is hight...";

global.set("DesiredStateLight", 0);

}

}

else {

if (global.get("DesiredStateLight") != 0) {

msg.topic = "Light Off by sheduler...";

msg.payload = 0;

}

}

break;

// Light On if Luminosity to low and it's day

case 4:

if (global.get("DayOrNight") == "Day")

{

if (global.get("LightLimit") > global.get("Luminosity")) {

msg.topic = "Light On because Brightness is low and it's Day...";

global.set("DesiredStateLight", 1);

}

else {

msg.topic = "Light Off because Brightness is hight... and it's Day";

global.set("DesiredStateLight", 0);

}

}

else

{

msg.topic = "Light Off because it's Night";

global.set("DesiredStateLight", 0);

}

break;

default:

break;

}

}

else

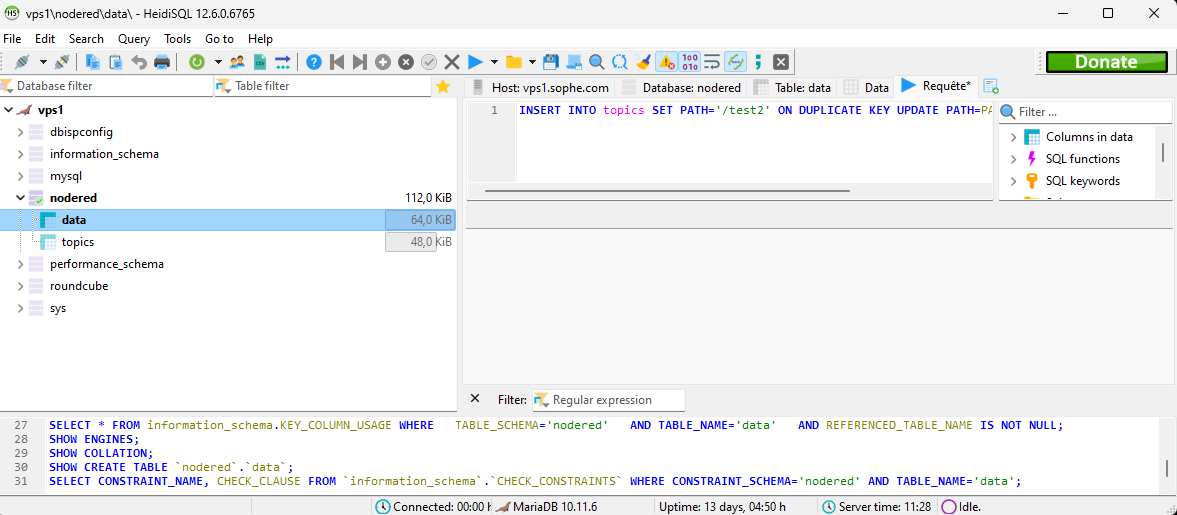
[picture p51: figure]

Page 14 sur 17

{

msg.topic = "Zigbee2mqtt or stm32 not active...";

}

msg.payload = global.get("DesiredStateLight");

return msg;

There are 5 operating modes.

Mode 0 : Manual mode, you can Light On/off with the button in dashboard.

Mode 1 : The light is On if the ambient brightness is to low.

Mode 2 : The Sheduler in Dashboard fix the state of the light.

Mode 3 : The sheduler in Dashboard fix the state of the light and the light is On if the ambient Brithness i slow.

Mode 4 : If it is Day and the light is on if the ambient Brithness i slow.

Part for UI Sheduler

DATABASE GROUP

The next step is to report the attributes values to a database of type Mariadb for persistence.

For working on windows with a good interface to Mysql or Mariadb, you can use this very good application heidisql : You can download here : https://www.heidisql.com/

This Group manage the persistence of attributes in database

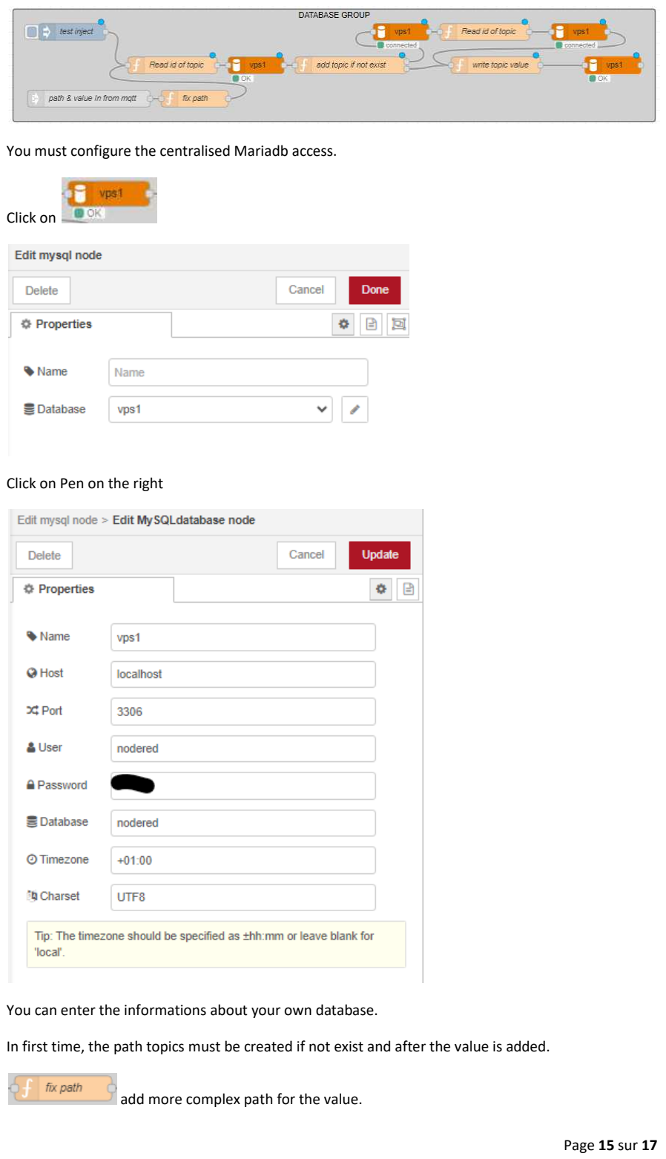
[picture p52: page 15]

Page 15 sur 17

You must configure the centralised Mariadb access.

Click on

Click on Pen on the right

You can enter the informations about your own database.

In first time, the path topics must be created if not exist and after the value is added.

add more complex path for the value.

Page 16 sur 17

It is necessary to send to DB link an event with msg.value wich contain the float numeric value to store and a msg.path path name for the value.

With this filter, the value is memorized and the database is used only if the new value has changed since the last one.

With no filter each value is stored.

The database use two tables for reducing the size of data storage :

- Topics table :
- Data table :

Sql source for create tables

CREATE TABLE IF NOT EXISTS `data` (
`idtopics` int(10) unsigned DEFAULT NULL,
`horodatage` timestamp(3) NULL DEFAULT current_timestamp(3) ON UPDATE current_timestamp(3), `value` double DEFAULT NULL,
KEY `Khorodatage` (`idtopics`,`horodatage`) USING BTREE,
) ENGINE=InnoDB DEFAULT CHARSET=utf8mb3 COLLATE=utf8mb3_general_ci;

CREATE TABLE IF NOT EXISTS `topics` (
`IdTopics` int(10) unsigned NOT NULL AUTO_INCREMENT,
`Path` varchar(255) DEFAULT NULL,
UNIQUE KEY `keyPath` (`Path`) USING BTREE,
KEY `FK_topics_data` (`IdTopics`)
) ENGINE=InnoDB AUTO_INCREMENT=1 DEFAULT CHARSET=utf8mb3 COLLATE=utf8mb3_general_ci;

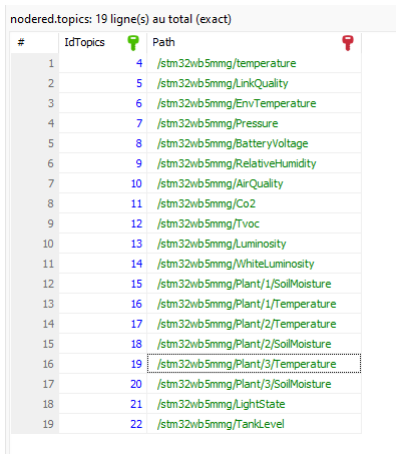
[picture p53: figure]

Page 17 sur 17

Now you have a persistence on selected attributes in a database.

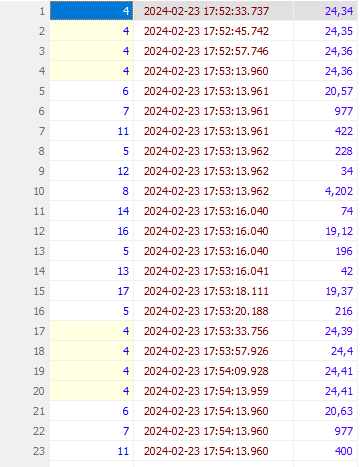
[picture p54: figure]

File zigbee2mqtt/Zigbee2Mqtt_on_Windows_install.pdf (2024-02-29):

### Installation and configuration of ZigbeetoMqtt on W

In first time, you must have an Zigbee Usb Adaptate

https://www.zigbee2mqtt.io/guide/adapters/

For me i use a Zigbee 3.0 USB adapter based on Silicon Labs EFR32MG21 with EZSP fine.


When you plug it you must find the good COM number.

For me COM3…

### Download & Install Node.js

Node.js is a library specialized in network and wri

You must download the last version here and execute

### Download & install zigbee2mqtt

This link is a good guide for installing.

https://www.zigbee2mqtt.io/guide/installation/05_wi

in my configuration the location of the zigbee2mqtt

c:\Users\<name user>\documents\zigbee2mqtt

in this directory you must configure data

### Installation and configuration of ZigbeetoMqtt on Windows 11

r compatible.

B adapter based on Silicon Labs EFR32MG21 with EZSP v8 from Aliexpress, which run

tten in javascript.

here and execute : https://nodejs.org/en

ndows.html

is here :

\configuration.yaml

Page 1 sur 14

### indows 11

v8 from Aliexpress, which run

Page

### 2 sur 14

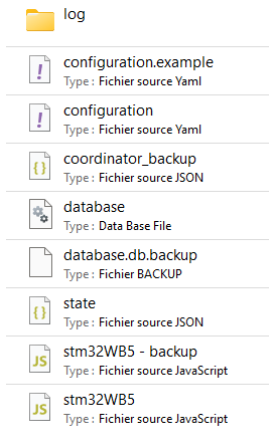
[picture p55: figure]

You must modify your configuration.yaml :

homeassistant: false
frontend: {}
mqtt:
server: mqtt://myserver.com:1883 base_topic: zigbee2mqtt
user: myuser
password: mypassword
force_disable_retain: false serial:
adapter: ezsp
port: \\.\COM3
advanced:
network_key:
- 217
- 145
- 238
- 190
- 25
- 53
- 239
- 2
- 252
- 99
- 160
- 200
- 244
- 205
- 243
- 38
pan_id: 23633
log_level: debug
log_syslog:
app_name: Zigbee2MQTT
eol: /n
host: localhost
localhost: localhost

Page 3 sur 14

path: /dev/log
pid: process.pid
port: 514
protocol: udp4
type: '5424'
channel: 15
homeassistant_legacy_entity_attributes: false legacy_api: false
legacy_availability_payload: false cache_state: false
output: attribute
external_converters:
- stm32WB5.js
device_options:
legacy: false
availability:
active:
# Time after which an active device will be marked as offline in # minutes (default = 10 minutes)

timeout: 5
passive:
# Time after which a passive device will be marked as offline in # minutes (default = 1500 minutes aka 25 hours)

timeout: 1500
devices:
# fix here address of your own card '0x0080e125006efe86':

friendly_name: STM32WB5MM-DK availability:
#every minute

timeout: 1
passlist:
# fix here address of your own card

- '0x0080e125006efe86'

In the mqtt part you specify the address of your server, the main topic to use, the username for this topic and the password. You can configure if necessary the certificates used for security.

In advanced : section you must add

Channel is the channel that zigbeetomqtt will listen to in my example, channel 15.

cache_state= false is very important, this prevents zigbee2mqtt from transmitting the olds values of the attributes each time with the one you are querying.

Output : attribute – generate one topic by attribute read.

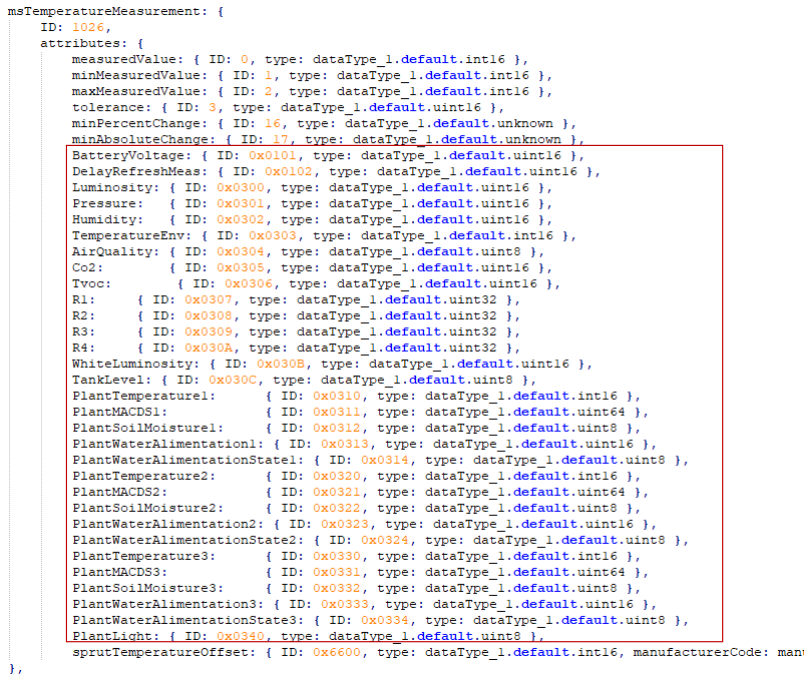
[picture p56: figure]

Page 4 sur 14

The stm32WB5.js file must be added in this same directory to reference the stm32wb5mm-dk card.

This configuration file will tell zigbee2mqtt:

fzL: List of attribute converters from the Zigbee network.

tzL: List of converters allowing you to transmit an attribute to a cluster id and attribute id or to query.

fz and tz: references the attributes of the standard.

e: Provision of attributes and display mode in the zigbee2mqtt interface.

My copy of this file is joined to this project.

Zigbee2mqtt have an web interface : zigbee-frontend. In the distribution this interface is compiled, but here it is necessary to add some attributes informations.

In file zigbee2mqtt/node_modules/zigbee-hersman/dist/zcl/definition/cluster.js

You must modify Cluster and add some attributes to Cluster 1026 :

In file zigbee2mqtt/node_modules/zigbee-herdsman-converters/lib/expose.js

You must modify and add

Page 5 sur 14

2 files are joins in the project.

### database and state Files of Zigbee2mqtt

In the file database you can find all entry of devices joined with Zigbee2mqtt.

If you want to make a new join procedure for a device, you must delete the correspondant line in this file.

And restart zigbee2mqtt and make a new join.

In the file stat, you can find in JSON format, the last value of exposed attributes for all devices.

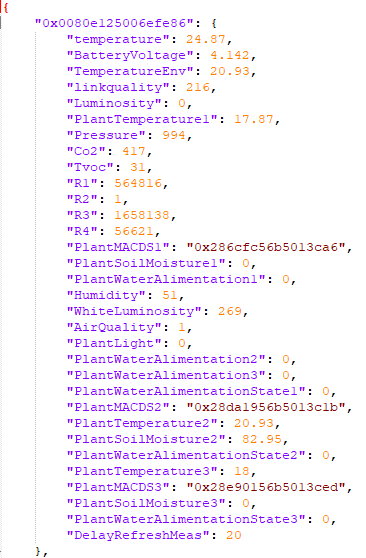
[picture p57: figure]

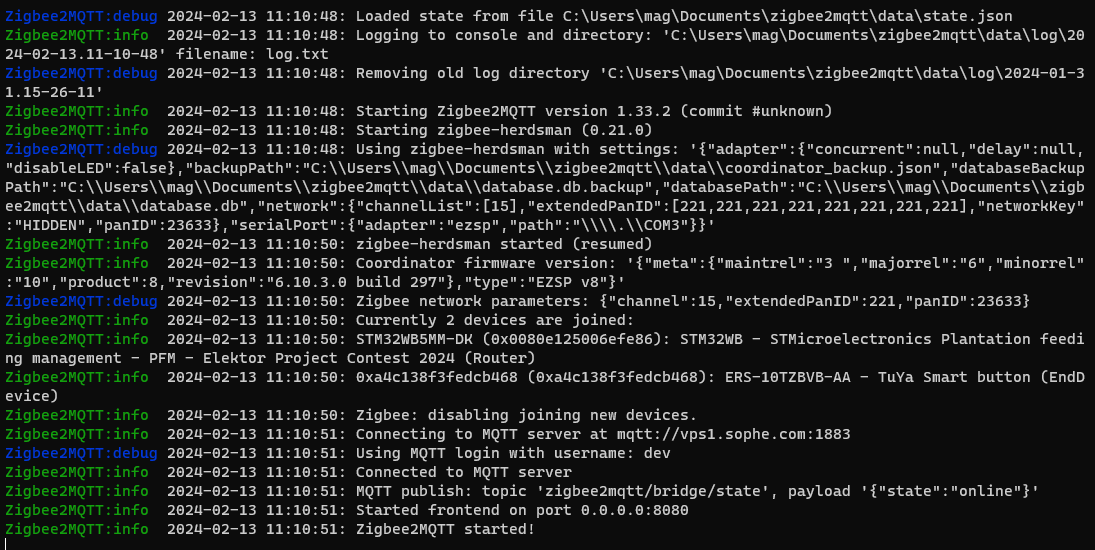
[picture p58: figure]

Page 6 sur 14

### Modify Zigbee-frontend

Zigbee2mqtt originally has a frontend interface, this interface is configured with standard Clusters and attributes. But if you wish to display and manage additional attributes in the drop-down menus, I will show you a procedure for updating the Front-end, which is compiled in the base distribution.

You must download the github zigbee2mqtt-frontend and compile the dist directory which will have to be placed in the zigbee2mqtt frontend plug-in.

Download the GitHub.

https://github.com/nurikk/zigbee2mqtt-frontend

you must update with the two precedents files.

- zigbee2mqtt-frontend/node_modules/zigbee-hersman/dist/zcl/definition/cluster.js
- zigbee2mqtt-frontend/node_modules/zigbee-herdsman-converters/lib/expose.js

In command mode, you compile with npm run build in zigbee2mqtt-frontend directory.

You must copy the complete directory zigbee2mqtt-frontend/dist to the directory to zigbee2mqtt/node_modules/zigbee2mqtt-frontend/dist

Now for starting, zigbeetomqtt write :

npm start in cmd mode from install directory.
When Zigbee2mqtt start, it try to contact the usb device and open the network. (Use CTRL + C for stopping or close the window).

Now you can have access to web gui interface of zigbee2mqtt on :

http://localhost:8080

when you want to make a new clean join for endpoint, you must erase the correspondant line in database.

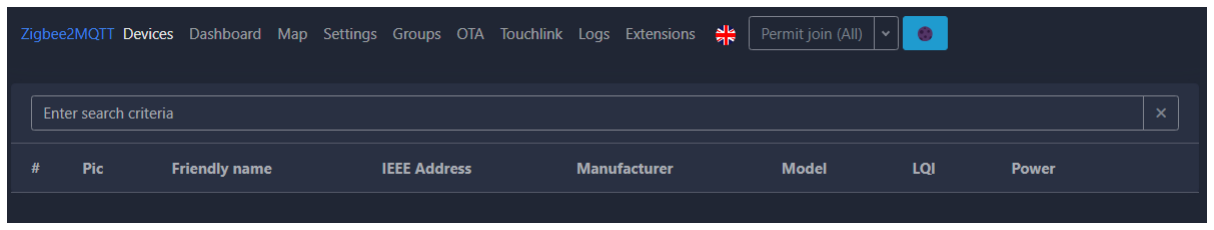
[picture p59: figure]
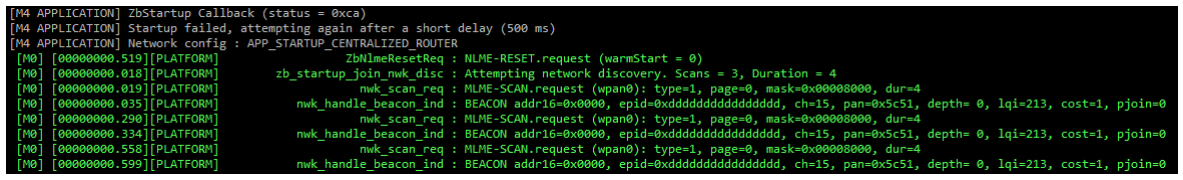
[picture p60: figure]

Page 7 sur 14

For forcing the card stm32wb5mm-dk to join the coordinator, you must press the button one (at left) and power on. You count 3 seconds and release the button.

A screen appears :

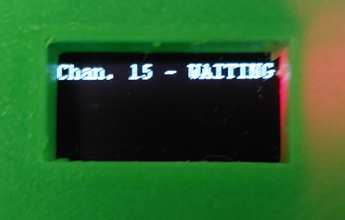
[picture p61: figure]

And the box try to rejoin the coordinator every 500ms.

You can click on Permi Join

### Join events

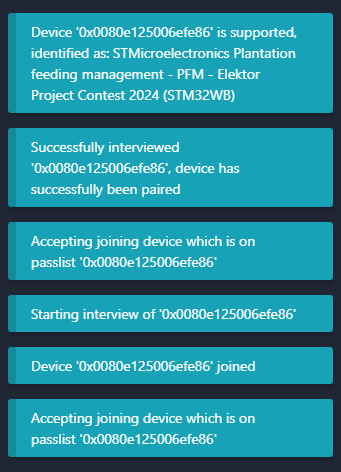
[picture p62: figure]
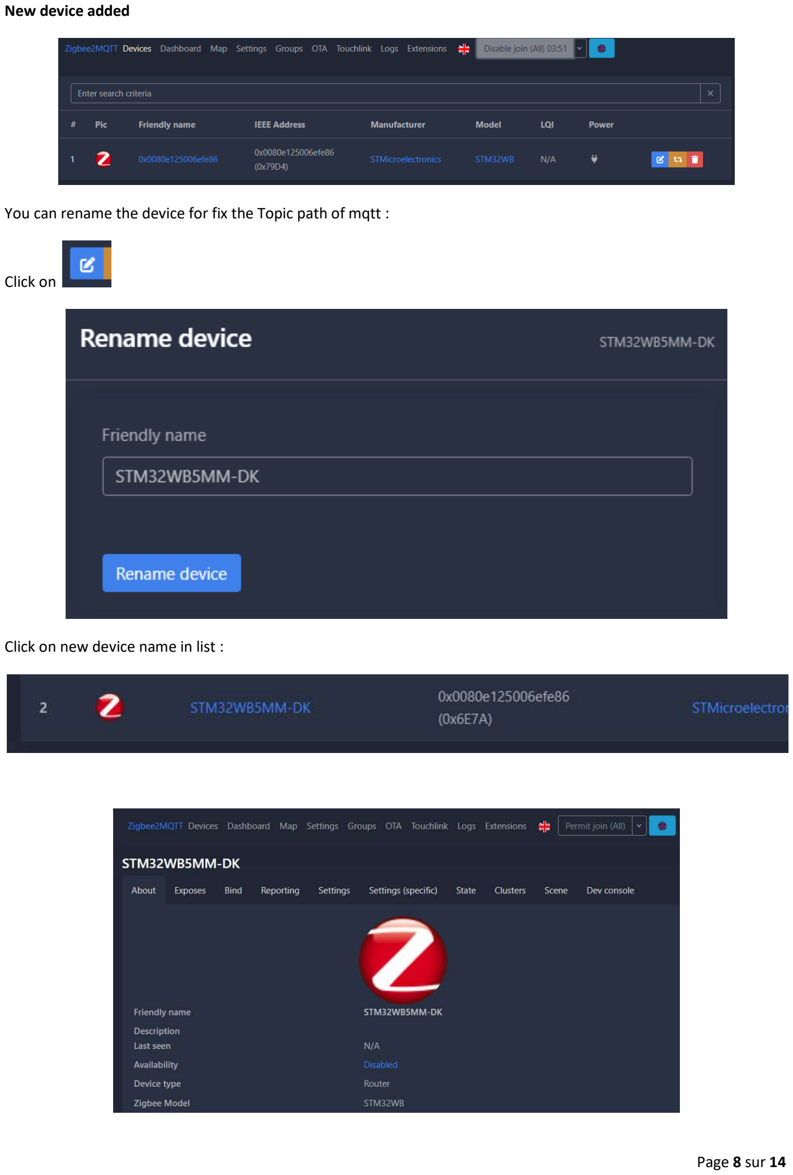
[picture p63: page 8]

Page 8 sur 14

New device added

You can rename the device for fix the Topic path of mqtt :

Click on

Click on new device name in list :

### Exposes Menu : View the list of attributes and last values

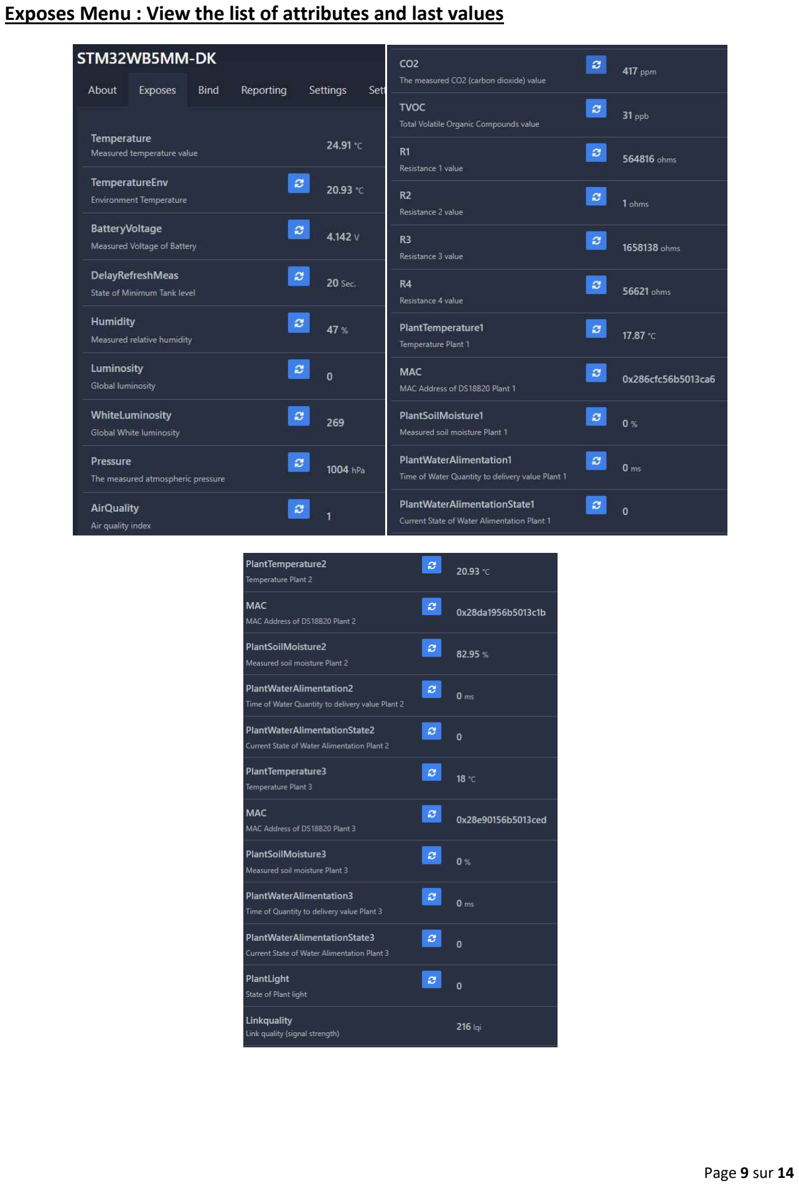
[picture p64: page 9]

Page 9 sur 14

Page 10 sur 14

### Clusters Menu

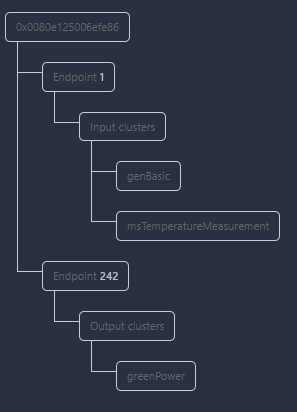
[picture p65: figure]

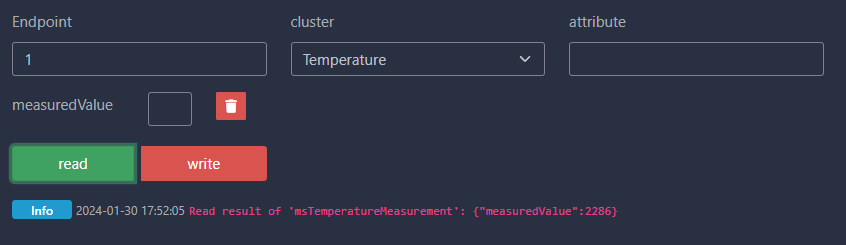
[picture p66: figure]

Page 11 sur 14

### Dev ConsoleMenu

In this console you can read or write value of attributes

For example : Read attribute Endpoint :1 Cluster :Temperature attribute : MeasuredValue

If you click on Read

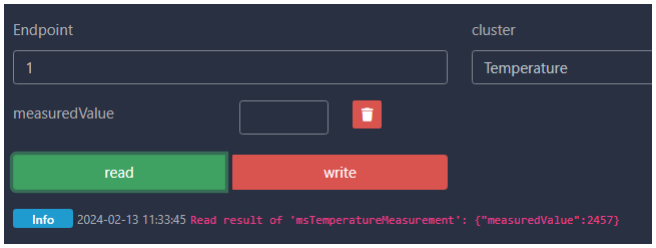
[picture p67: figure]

The answer in console windows :

You can observe that :

- A mqtt request has sent to the MQTT Topic: zigbee2mqtt/STM32WB5MM-DK/1/set
- with JSON payload :

{"read":{"attributes":["measuredValue"],"cluster":"msTemperatureMeasurement","options":{}}}
- Zigbee2mqtt transform in : Publishing 'set' 'read' to 'STM32WB5MM-DK'
- Zigbee2mqtt receive :

Received Zigbee message from 'STM32WB5MM-DK', type 'readResponse', cluster 'msTemperatureMeasurement', data '{"measuredValue":2457}' from endpoint 1 with groupID 0
- Zigbee2mqtt send 2 topics for Mqtt server :

MQTT publish: topic 'zigbee2mqtt/STM32WB5MM-DK/temperature', payload '24.57'
MQTT publish: topic 'zigbee2mqtt/STM32WB5MM-DK/linkquality', payload '212'

### You can Read multiples attributes :

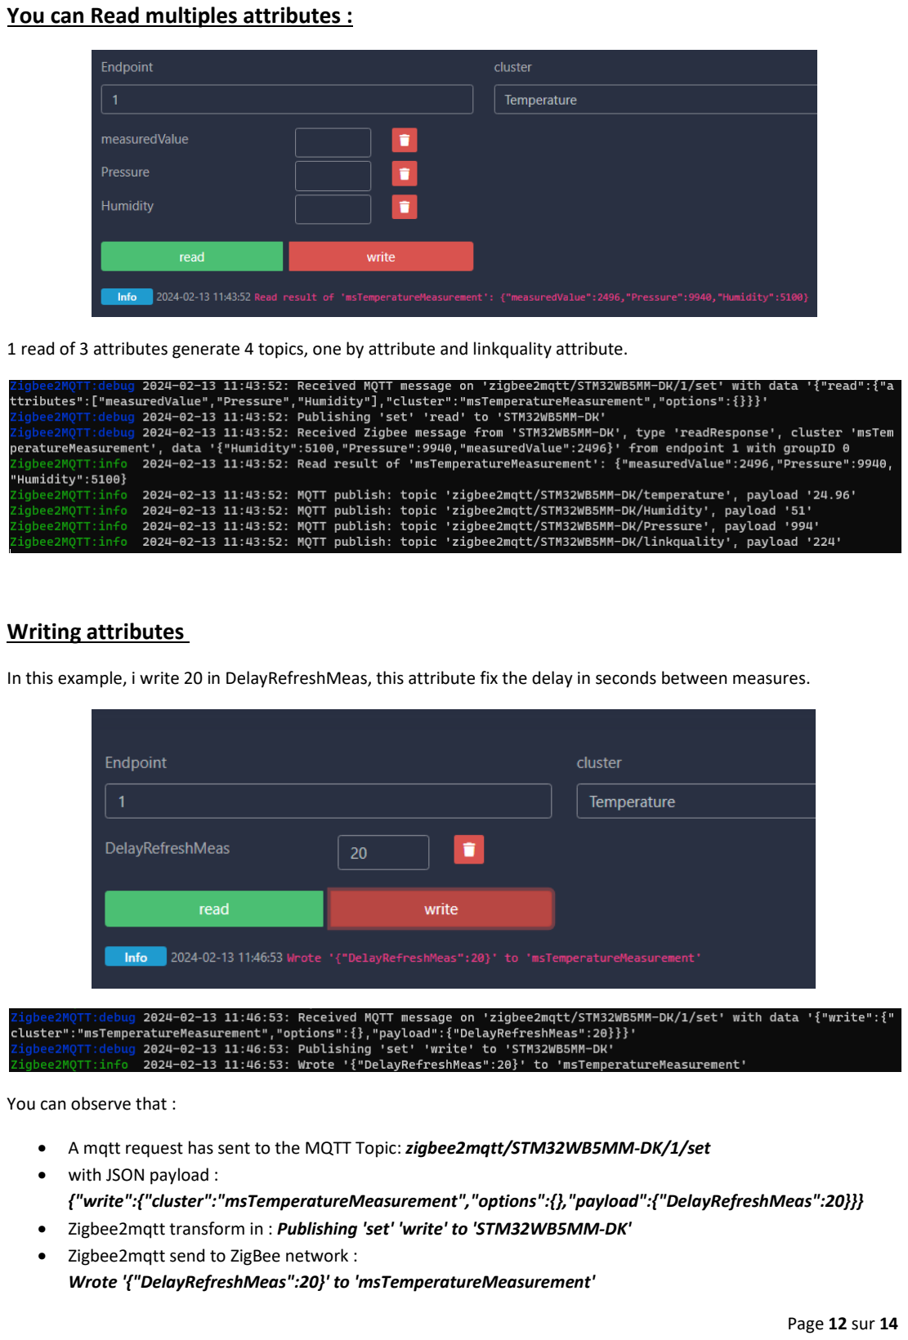
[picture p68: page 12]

Page 12 sur 14

1 read of 3 attributes generate 4 topics, one by attribute and linkquality attribute.

### Writing attributes

In this example, i write 20 in DelayRefreshMeas, this attribute fix the delay in seconds between measures.

You can observe that :

- A mqtt request has sent to the MQTT Topic: zigbee2mqtt/STM32WB5MM-DK/1/set
- with JSON payload :

{"write":{"cluster":"msTemperatureMeasurement","options":{},"payload":{"DelayRefreshMeas":20}}}
- Zigbee2mqtt transform in : Publishing 'set' 'write' to 'STM32WB5MM-DK'
- Zigbee2mqtt send to ZigBee network :

Wrote '{"DelayRefreshMeas":20}' to 'msTemperatureMeasurement'

### Test reporting

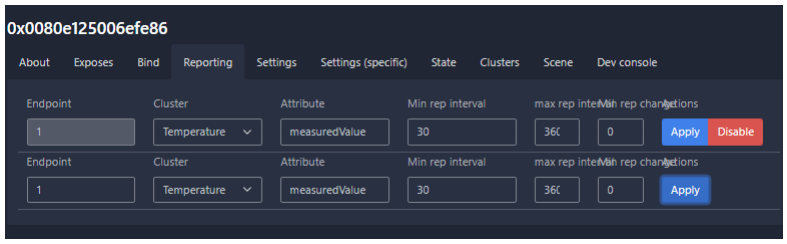
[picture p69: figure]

After apply

- A mqtt request has sent to the MQTT Topic:

zigbee2mqtt/bridge/request/device/configure_reporti
- with JSON payload :

{"attribute":"measuredValue","cluster":"msTemperatu DK/1","maximum_report_interval":3600,"minimum_report_interval":60,"repo "transaction":"okbmi-8"}'

In response

- A mqtt request has sent to the MQTT Topic:

zigbee2mqtt/bridge/request/device/configure_reporti
- with JSON payload :

'{"data":{"attribute":"measured DK/1","maximum_report_interval":3600,"minimum_repor "ok","transaction":"okbmi-8"}'

It is the same payload sent but "status"

Report every 30s

ng

reMeasurement","id":"STM32WB5MM t_interval":3600,"minimum_report_interval":60,"repo

ng

Value","cluster":"msTemperatureMeasurement","id":"S t_interval":60,"reportable_change":0},"status":

added with "ok" or "error".

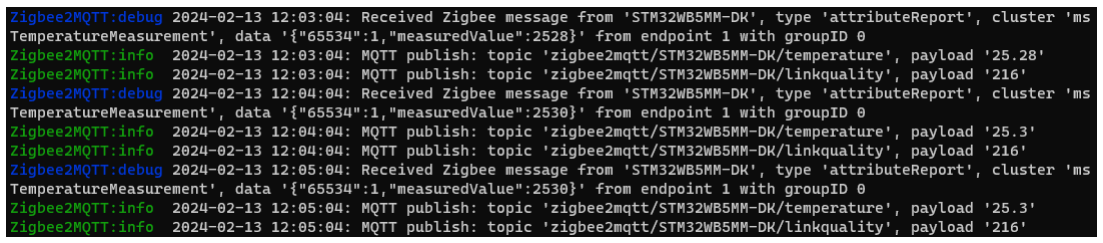
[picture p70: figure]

Page 13 sur 14

rtable_change":0,

TM32WB5MM-

Page 14 sur 14

### CONCLUSION

It is very easy now to interact with the Zigbee Device using Mqtt Request.

The stm32wb55 processor is a good solution which correctly manages the Zigbee standard.

The next part is now to configure and use Node-RED application for automation, data storage and visualisation of informations.

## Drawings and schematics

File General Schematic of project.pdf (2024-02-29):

# GENERAL MAP OF PROJECT - ELEKTOR STM32 Wireless Innovaon Design Contest 2024

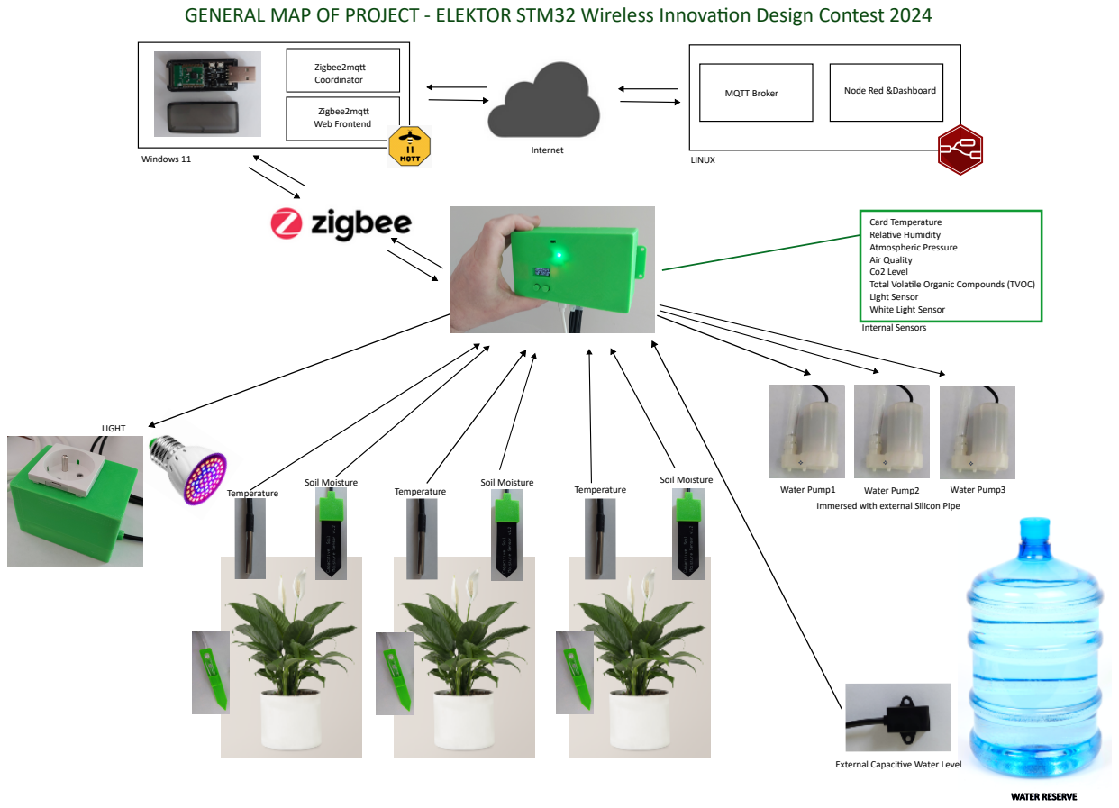
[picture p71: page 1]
WATER RESERVE; Soil Moisture; Temperature; LIGHT; Water Pump1; Water Pump2; Water Pump3; Zigbee2mq Coordinator; Zigbee2mq Web Frontend; Windows 11; LINUX; MQTT Broker; Node Red &Dashboard; Internet

Card Temperature
Relave Humidity
Atmospheric Pressure
Air Quality
Co2 Level
Total Volale Organic Compounds (TVOC)
Light Sensor
White Light Sensor
Internal Sensors

Immersed with external Silicon Pipe

External Capacive Water Level

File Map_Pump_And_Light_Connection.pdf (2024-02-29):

## MAP OF CONNECTIONS WITH POWER MODULE AND LIGHT COMMAND

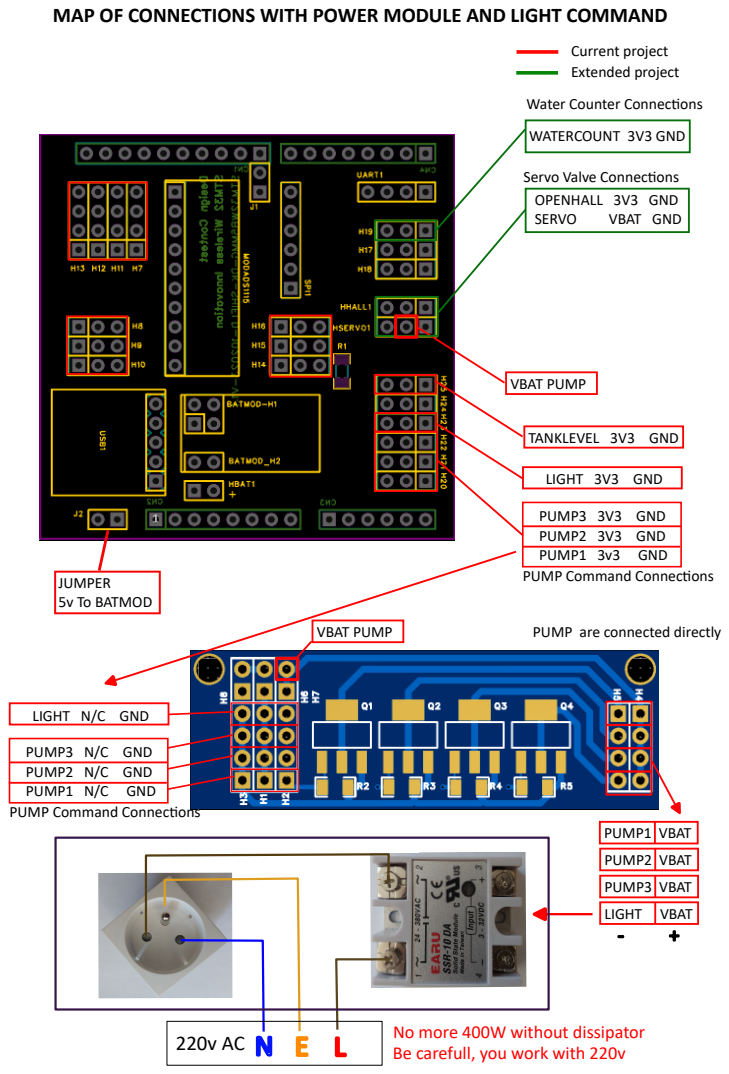
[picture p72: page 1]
JUMPER 5v To BATMOD; Current project; SERVO; VBAT GND; WATERCOUNT 3V3 GND; LIGHT 3V3 GND; LIGHT N/C GND; TANKLEVEL 3V3 GND; VBAT PUMP; PUMP1; VBAT; Extended project; PUMP2; PUMP3; LIGHT; No more 400W without dissipator

Water Counter Connecons

Servo Valve Connecons
OPENHALL 3V3 GND

PUMP3 3V3 GND
PUMP2 3V3 GND
PUMP1 3v3 GND
PUMP Command Connecons

PUMP are connected directly

PUMP3 N/C GND
PUMP2 N/C GND
PUMP1 N/C GND

Be carefull, you work with 220v

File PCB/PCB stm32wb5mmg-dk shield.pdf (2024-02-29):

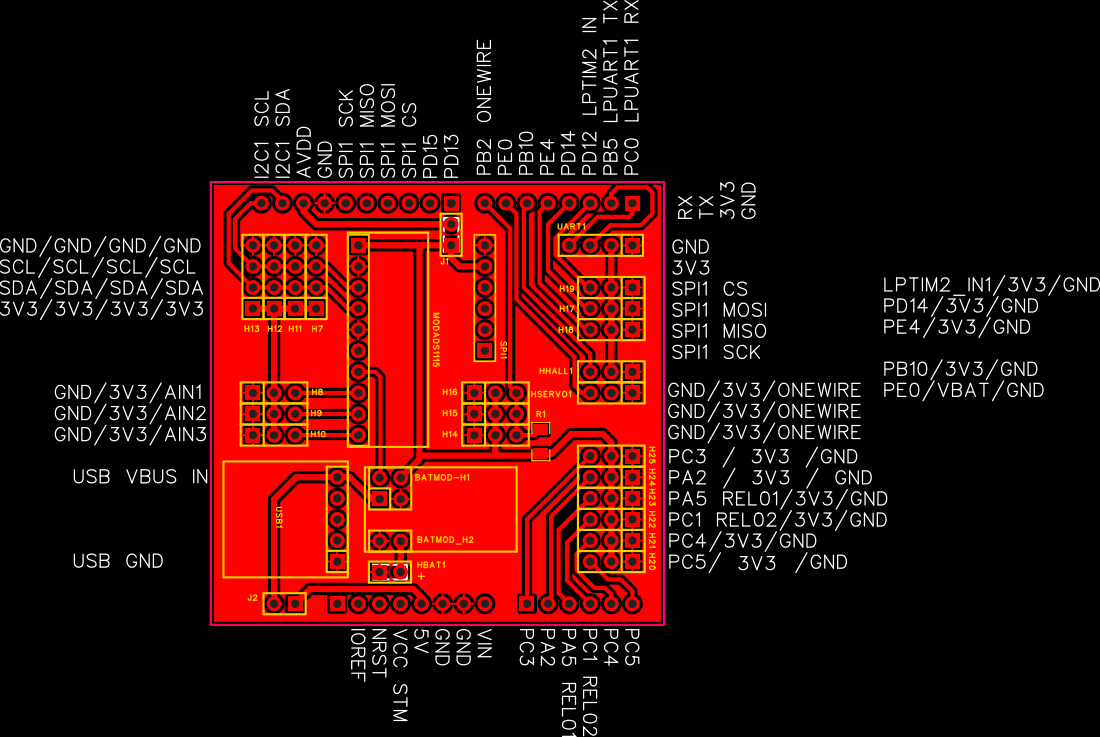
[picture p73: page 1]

GND/GND/GND/GNDSCL/SCL/SCL/SCLSDA/SDA/SDA/SDA3V3/3V3/3V3/3V3

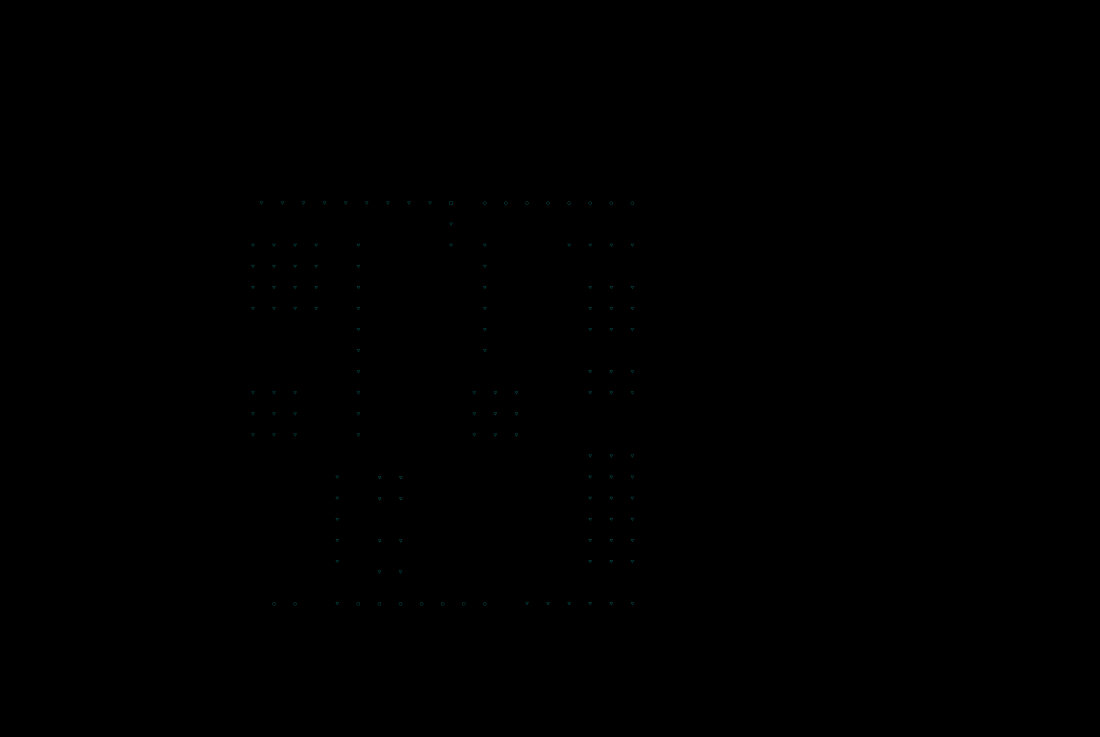
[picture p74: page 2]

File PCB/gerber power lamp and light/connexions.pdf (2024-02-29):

GND/VBAT/CMDLAMPGND/VBAT/CMDPUMP3 POWERPUMP1/VIN GND/VBAT/CMDPUMP2 POWERPUMP2/VIN GND/VBAT/CMDPUMP1 POWERPUMP3/VINPOWERLAMP/VIN

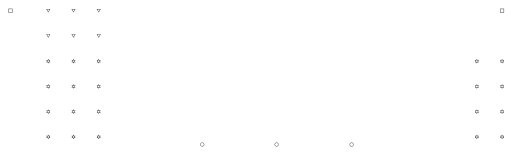
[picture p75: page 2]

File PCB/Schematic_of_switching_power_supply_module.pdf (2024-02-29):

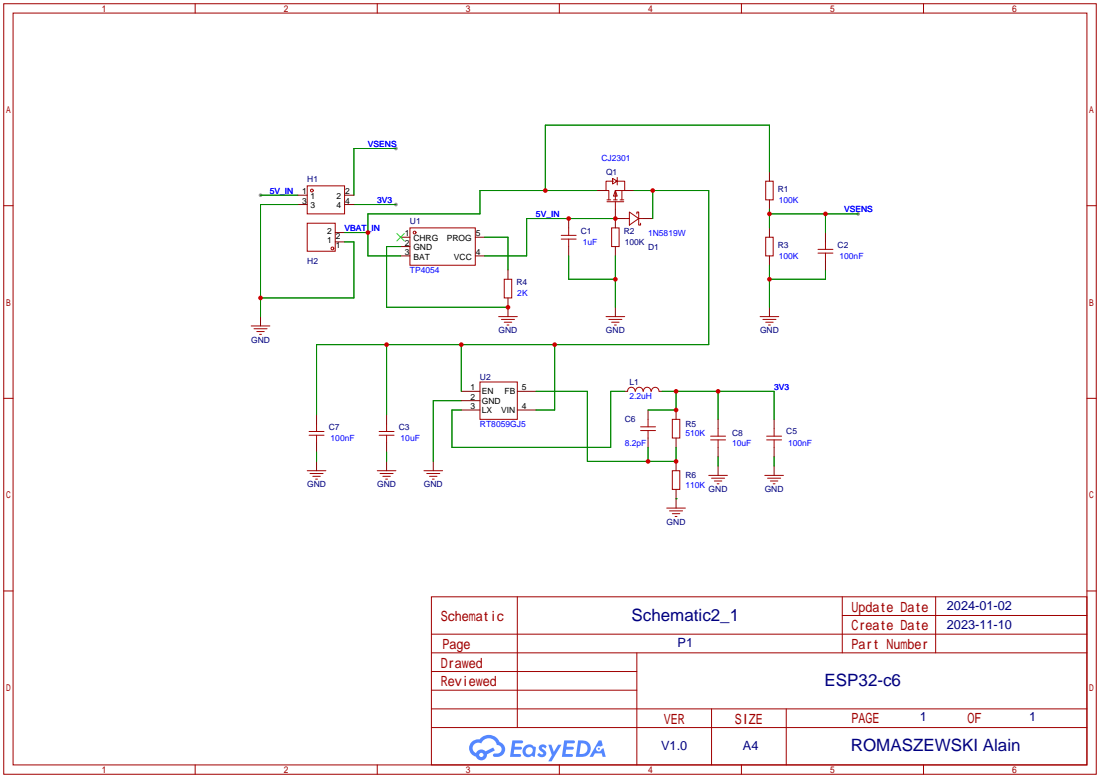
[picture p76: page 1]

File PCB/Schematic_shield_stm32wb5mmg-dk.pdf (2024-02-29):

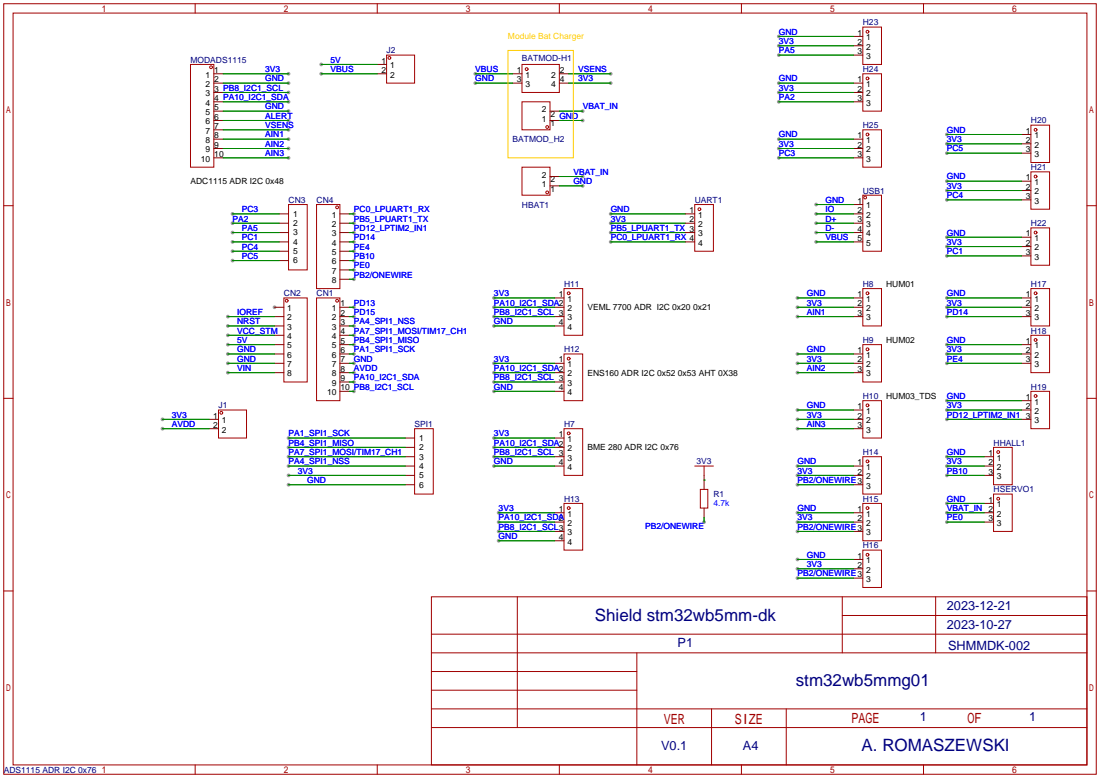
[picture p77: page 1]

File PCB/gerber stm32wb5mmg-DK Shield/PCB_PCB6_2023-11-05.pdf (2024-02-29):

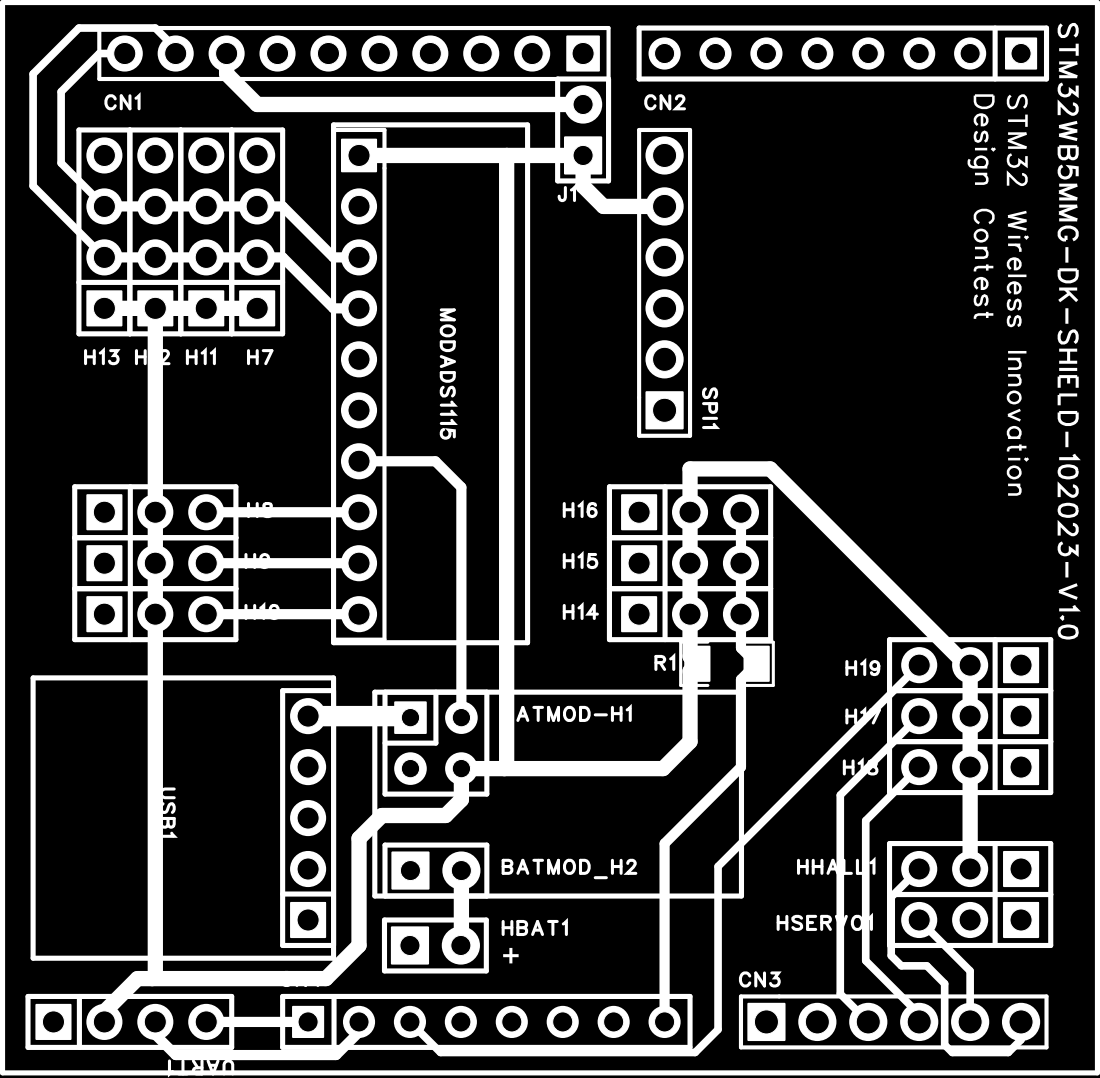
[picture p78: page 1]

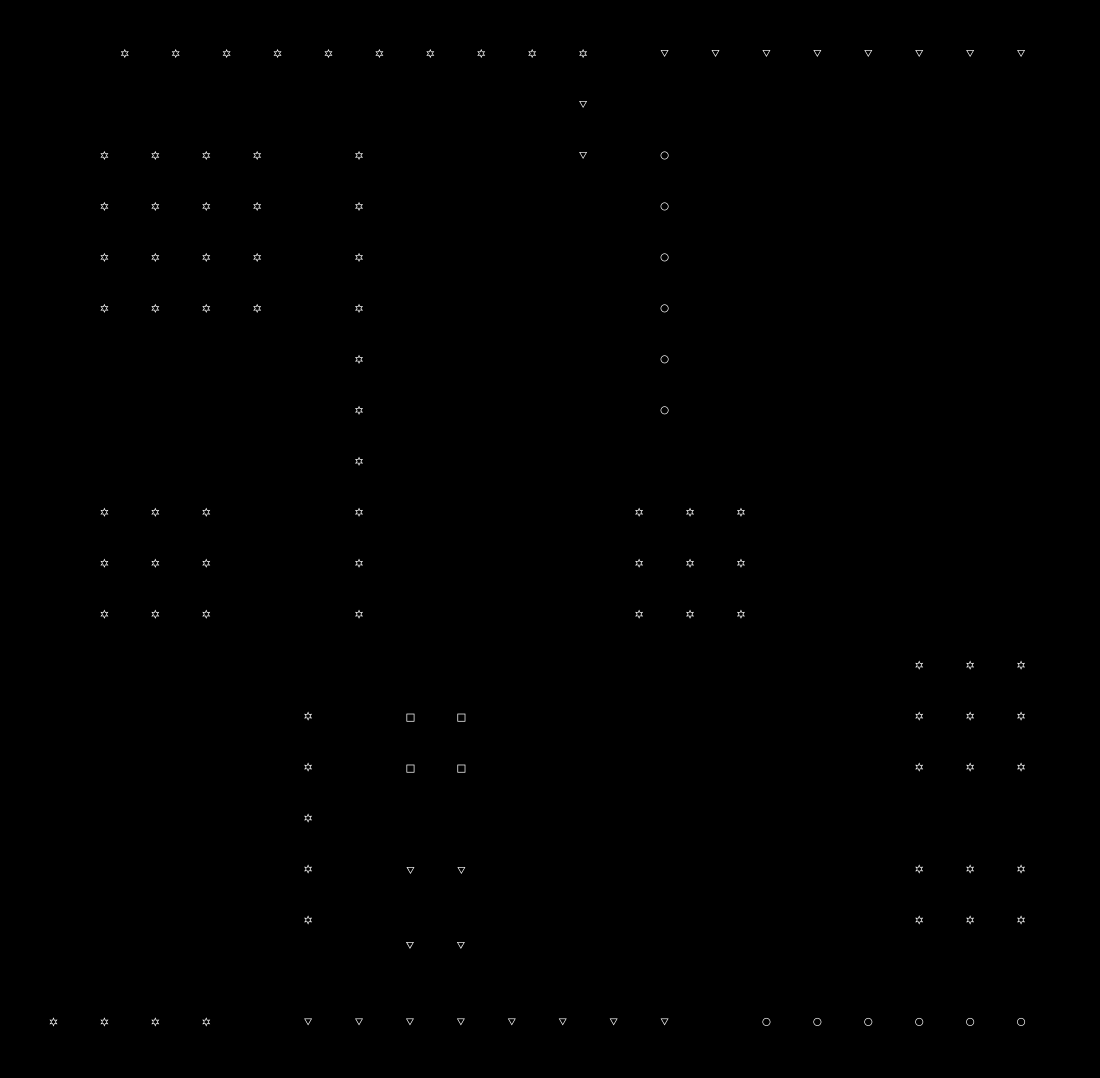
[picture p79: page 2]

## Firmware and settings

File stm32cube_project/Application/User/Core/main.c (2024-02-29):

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
/* Includes ------------------------------------------------------------------*/
#include "main.h"

/* USER CODE BEGIN Includes */

#include "dbg_trace.h"
#include "hw_conf.h"
#include "otp.h"
#include "stm32_seq.h"

/* USER CODE END Includes */

IPCC_HandleTypeDef hipcc;

UART_HandleTypeDef hlpuart1;
UART_HandleTypeDef huart1;
DMA_HandleTypeDef hdma_lpuart1_tx;
DMA_HandleTypeDef hdma_usart1_tx;
I2C_HandleTypeDef hi2c1;
I2C_HandleTypeDef hi2c3;

RTC_HandleTypeDef hrtc;

void SystemClock_Config(void);
static void MX_GPIO_Init(void);
static void MX_DMA_Init(void);
static void MX_RF_Init(void);
static void MX_RTC_Init(void);
static void MX_IPCC_Init(void);
/* USER CODE BEGIN PFP */

void PeriphClock_Config(void);
static void Reset_Device(void);
static void Reset_IPCC(void);
static void Reset_BackupDomain(void);
static void Init_Exti(void);
static void Config_HSE(void);
static void MX_I2C1_Init(void);
static void MX_I2C3_Init(void);

/* USER CODE END PFP */

/**
  * @brief  The application entry point.
  * @retval int
  */
int main(void)
{
  /* USER CODE BEGIN 1 */

  /**
   * The OPTVERR flag is wrongly set at power on
   * It shall be cleared before using any HAL_FLASH_xxx() api
   */
  __HAL_FLASH_CLEAR_FLAG(FLASH_FLAG_OPTVERR);

  /* USER CODE END 1 */

  /* MCU Configuration--------------------------------------------------------*/

  /* Reset of all peripherals, Initializes the Flash interface and the Systick. */
  HAL_Init();

  /* USER CODE BEGIN Init */
  
  Reset_Device();
  Config_HSE();
  
  /* USER CODE END Init */

  /* Configure the system clock */
  SystemClock_Config();

  /* IPCC initialisation */
   MX_IPCC_Init();

  /* USER CODE BEGIN SysInit */
  PeriphClock_Config();
  Init_Exti(); /**< Configure the system Power Mode */
  /* USER CODE END SysInit */

  /* Initialize all configured peripherals */
  MX_GPIO_Init();
  MX_DMA_Init();
  MX_RF_Init();
  MX_RTC_Init();
  //MX_I2C1_Init();
  MX_I2C3_Init();
  /* Init code for STM32_WPAN */
  APPE_Init();
  /* Infinite loop */
  /* USER CODE BEGIN WHILE */
  while (1)
  {
    UTIL_SEQ_Run( UTIL_SEQ_DEFAULT );
    /* USER CODE END WHILE */

    /* USER CODE BEGIN 3 */
  }
  /* USER CODE END 3 */
}

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
/* USER CODE BEGIN 4 */
void PeriphClock_Config(void)
{
  #if (CFG_USB_INTERFACE_ENABLE != 0)
  RCC_PeriphCLKInitTypeDef PeriphClkInitStruct = { 0 };
  RCC_CRSInitTypeDef RCC_CRSInitStruct = { 0 };

  /**
   * This prevents the CPU2 to disable the HSI48 oscillator when
   * it does not use anymore the RNG IP
   */
  LL_HSEM_1StepLock( HSEM, 5 );

  LL_RCC_HSI48_Enable();

  while(!LL_RCC_HSI48_IsReady());

  /* Select HSI48 as USB clock source */
  PeriphClkInitStruct.PeriphClockSelection = RCC_PERIPHCLK_USB;
  PeriphClkInitStruct.UsbClockSelection = RCC_USBCLKSOURCE_HSI48;
  HAL_RCCEx_PeriphCLKConfig(&PeriphClkInitStruct);

  /*Configure the clock recovery system (CRS)**********************************/

  /* Enable CRS Clock */
  __HAL_RCC_CRS_CLK_ENABLE();

  /* Default Synchro Signal division factor (not divided) */
  RCC_CRSInitStruct.Prescaler = RCC_CRS_SYNC_DIV1;

  /* Set the SYNCSRC[1:0] bits according to CRS_Source value */
  RCC_CRSInitStruct.Source = RCC_CRS_SYNC_SOURCE_USB;

  /* HSI48 is synchronized with USB SOF at 1KHz rate */
  RCC_CRSInitStruct.ReloadValue = RCC_CRS_RELOADVALUE_DEFAULT;
  RCC_CRSInitStruct.ErrorLimitValue = RCC_CRS_ERRORLIMIT_DEFAULT;

  RCC_CRSInitStruct.Polarity = RCC_CRS_SYNC_POLARITY_RISING;

  /* Set the TRIM[5:0] to the default value*/
  RCC_CRSInitStruct.HSI48CalibrationValue = RCC_CRS_HSI48CALIBRATION_DEFAULT;

  /* Start automatic synchronization */
  HAL_RCCEx_CRSConfig(&RCC_CRSInitStruct);
#endif

  return;
}

/*************************************************************
 *
 * LOCAL FUNCTIONS
 *
 *************************************************************/

static void Config_HSE(void)
{
    OTP_ID0_t * p_otp;

  /**
   * Read HSE_Tuning from OTP
   */
  p_otp = (OTP_ID0_t *) OTP_Read(0);
  if (p_otp)
  {
    LL_RCC_HSE_SetCapacitorTuning(p_otp->hse_tuning);
  }

  return;
}


static void Reset_Device( void )
{
#if ( CFG_HW_RESET_BY_FW == 1 )
  Reset_BackupDomain();

  Reset_IPCC();
#endif

  return;
}

static void Reset_IPCC( void )
{
  LL_AHB3_GRP1_EnableClock(LL_AHB3_GRP1_PERIPH_IPCC);

  LL_C1_IPCC_ClearFlag_CHx(
      IPCC,
      LL_IPCC_CHANNEL_1 | LL_IPCC_CHANNEL_2 | LL_IPCC_CHANNEL_3 | LL_IPCC_CHANNEL_4
      | LL_IPCC_CHANNEL_5 | LL_IPCC_CHANNEL_6);

  LL_C2_IPCC_ClearFlag_CHx(
      IPCC,
      LL_IPCC_CHANNEL_1 | LL_IPCC_CHANNEL_2 | LL_IPCC_CHANNEL_3 | LL_IPCC_CHANNEL_4
      | LL_IPCC_CHANNEL_5 | LL_IPCC_CHANNEL_6);

  LL_C1_IPCC_DisableTransmitChannel(
      IPCC,
      LL_IPCC_CHANNEL_1 | LL_IPCC_CHANNEL_2 | LL_IPCC_CHANNEL_3 | LL_IPCC_CHANNEL_4
      | LL_IPCC_CHANNEL_5 | LL_IPCC_CHANNEL_6);

  LL_C2_IPCC_DisableTransmitChannel(
      IPCC,
      LL_IPCC_CHANNEL_1 | LL_IPCC_CHANNEL_2 | LL_IPCC_CHANNEL_3 | LL_IPCC_CHANNEL_4
      | LL_IPCC_CHANNEL_5 | LL_IPCC_CHANNEL_6);

  LL_C1_IPCC_DisableReceiveChannel(
      IPCC,
      LL_IPCC_CHANNEL_1 | LL_IPCC_CHANNEL_2 | LL_IPCC_CHANNEL_3 | LL_IPCC_CHANNEL_4
      | LL_IPCC_CHANNEL_5 | LL_IPCC_CHANNEL_6);

  LL_C2_IPCC_DisableReceiveChannel(
      IPCC,
      LL_IPCC_CHANNEL_1 | LL_IPCC_CHANNEL_2 | LL_IPCC_CHANNEL_3 | LL_IPCC_CHANNEL_4
      | LL_IPCC_CHANNEL_5 | LL_IPCC_CHANNEL_6);

  return;
}

static void Reset_BackupDomain( void )
{
  if ((LL_RCC_IsActiveFlag_PINRST() != FALSE) && (LL_RCC_IsActiveFlag_SFTRST() == FALSE))
  {
    HAL_PWR_EnableBkUpAccess(); /**< Enable access to the RTC registers */

    /**
     *  Write twice the value to flush the APB-AHB bridge
     *  This bit shall be written in the register before writing the next one
     */
    HAL_PWR_EnableBkUpAccess();

    __HAL_RCC_BACKUPRESET_FORCE();
    __HAL_RCC_BACKUPRESET_RELEASE();
  }

  return;
}

static void Init_Exti( void )
{
  /* Enable IPCC(36), HSEM(38) wakeup interrupts on CPU1 */
  LL_EXTI_EnableIT_32_63(LL_EXTI_LINE_36 | LL_EXTI_LINE_38);

  return;
}

/*************************************************************
 *
 * WRAP FUNCTIONS
 *
 *************************************************************/
void HAL_Delay(uint32_t Delay)
{
  uint32_t tickstart = HAL_GetTick();
  uint32_t wait = Delay;

  /* Add a freq to guarantee minimum wait */
  if (wait < HAL_MAX_DELAY)
  {
    wait += HAL_GetTickFreq();
  }

  while ((HAL_GetTick() - tickstart) < wait)
  {
    /************************************************************************************
     * ENTER SLEEP MODE
     ***********************************************************************************/
    LL_LPM_EnableSleep( ); /**< Clear SLEEPDEEP bit of Cortex System Control Register */

    /**
     * This option is used to ensure that store operations are completed
     */
  #if defined ( __CC_ARM)
    __force_stores();
  #endif

    __WFI( );
  }
}

/* USER CODE END 4 */
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


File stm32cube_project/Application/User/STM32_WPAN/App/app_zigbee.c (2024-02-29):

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

/* Includes ------------------------------------------------------------------*/
#include "app_common.h"
#include "app_entry.h"
#include "dbg_trace.h"
#include "app_zigbee.h"
#include "zigbee_interface.h"
#include "shci.h"
#include "stm_logging.h"
#include "app_conf.h"
#include "app_stts22h.h"
#include "stm32wbxx_core_interface_def.h"
#include "zigbee_types.h"
#include "stm32_seq.h"
#include "ee.h"
#include "hw_flash.h"

#include <assert.h>
#include "zcl/zcl.h"
#include "zcl/general/zcl.temp.meas.h"
#include "zcl/general/zcl.wcm.h"
#include "app_clusters.h"
#include "app_ScheduleMeasure.h"
#include "app_screen.h"

#define CFG_NVM                 1U /* use FLASH */
#define CFG_NVM_DIAG            1U

#define APP_ZIGBEE_STARTUP_FAIL_DELAY               500U
#define CHANNEL                                     15

#define SW1_ENDPOINT                                17
#define SW2_ENDPOINT                                30

/* USER CODE BEGIN PD */
#define SW1_GROUP_ADDR          0x0001
#define MIN_MEASURED_TEMP       0xf060   /* -40C   */
#define MAX_MEASURED_TEMP       0x30d4   /* 125C   */
#define TOLERANCE_TEMP          0x0032   /* +-0.5C */
#define MIN_HUM					0x0000  /* 0% */
#define MAX_HUM					0x2710  /* 100% */

/* USER CODE END PD */

/* External definition -------------------------------------------------------*/
enum ZbStatusCodeT ZbStartupWait(struct ZigBeeT *zb, struct ZbStartupT *config);

static void APP_ZIGBEE_StackLayersInit(void);
static void APP_ZIGBEE_ConfigEndpoints(void);
static void APP_ZIGBEE_NwkForm(void);
static void APP_ZIGBEE_TraceError(const char *pMess, uint32_t ErrCode);
static void APP_ZIGBEE_CheckWirelessFirmwareInfo(void);
static void Wait_Getting_Ack_From_M0(void);
static void Receive_Ack_From_M0(void);
static void Receive_Notification_From_M0(void);
static void APP_ZIGBEE_ProcessNotifyM0ToM4(void);
static void APP_ZIGBEE_ProcessRequestM0ToM4(void);

static bool APP_ZIGBEE_persist_load(void);
static bool APP_ZIGBEE_persist_save(void);
static void APP_ZIGBEE_persist_delete(void);
static void APP_ZIGBEE_persist_notify_cb(struct ZigBeeT *zb, void *cbarg);
static enum ZbStatusCodeT APP_ZIGBEE_ZbStartupPersist(struct ZigBeeT *zb);
static void APP_ZIGBEE_PersistCompleted_callback(enum ZbStatusCodeT status,void *arg);
//static enum ZclStatusCodeT APP_ZIGBEE_RestoreClusterAttr(struct ZbZclClusterT *clusterPtr);
#ifdef CFG_NVM
static void APP_ZIGBEE_NVM_Init(void);
static bool APP_ZIGBEE_NVM_Read(void);
static bool APP_ZIGBEE_NVM_Write(void);
static void APP_ZIGBEE_NVM_Erase(void);
#endif /* CFG_NVM */
static void APP_ZIGBEE_NVM_Diag_Init(void);
static void APP_ZIGBEE_NVM_Diag_Exec(void);
static bool APP_ZIGBEE_NVM_Diag_DataValidation(void);

static void LED_On(aPwmLedGsData_TypeDef aPwmLedGsData);
static void LED_Off(void);
static void LED_Deinit(void);
static void LED_Toggle(aPwmLedGsData_TypeDef aPwmLedGsData);
/* USER CODE BEGIN PFP */
static void APP_ZIGBEE_ConfigGroupAddr(void);
/* USER CODE END PFP */

static TL_CmdPacket_t *p_ZIGBEE_otcmdbuffer;
static TL_EvtPacket_t *p_ZIGBEE_notif_M0_to_M4;
static TL_EvtPacket_t *p_ZIGBEE_request_M0_to_M4;
static __IO uint32_t CptReceiveNotifyFromM0 = 0;
static __IO uint32_t CptReceiveRequestFromM0 = 0;

PLACE_IN_SECTION("MB_MEM1") ALIGN(4) static TL_ZIGBEE_Config_t ZigbeeConfigBuffer;
PLACE_IN_SECTION("MB_MEM2") ALIGN(4) static TL_CmdPacket_t ZigbeeOtCmdBuffer;
PLACE_IN_SECTION("MB_MEM2") ALIGN(4) static uint8_t ZigbeeNotifRspEvtBuffer[sizeof(TL_PacketHeader_t) + TL_EVT_HDR_SIZE + 255U];
PLACE_IN_SECTION("MB_MEM2") ALIGN(4) static uint8_t ZigbeeNotifRequestBuffer[sizeof(TL_PacketHeader_t) + TL_EVT_HDR_SIZE + 255U];


struct zigbee_app_info zigbee_app_info;


/* NVM variables */
/* cache in uninit RAM to store/retrieve persistent data */
union cache
{
  uint8_t  U8_data[ST_PERSIST_MAX_ALLOC_SZ];     // in bytes
  uint32_t U32_data[ST_PERSIST_MAX_ALLOC_SZ/4U]; // in U32 words
};
// __attribute__ ((section(".noinit"))) union cache cache_persistent_data;

// __attribute__ ((section(".noinit"))) union cache cache_diag_reference;

union cache cache_persistent_data;
union cache cache_diag_reference;


/* timer to delay reading attribute back from persistence */
//static uint8_t TS_ID1;
//static uint8_t TS_ID2;
/* Functions Definition ------------------------------------------------------*/



/**
 * @brief  Zigbee application initialization
 * @param  None
 * @retval None
 */
void APP_ZIGBEE_Init(void)
{
  SHCI_CmdStatus_t ZigbeeInitStatus;

  APP_DBG("APP_ZIGBEE_Init");
  LED_Off();
  /* Check the compatibility with the Coprocessor Wireless Firmware loaded */
  APP_ZIGBEE_CheckWirelessFirmwareInfo();

  /* Register cmdbuffer */
  APP_ZIGBEE_RegisterCmdBuffer(&ZigbeeOtCmdBuffer);

  /* Init config buffer and call TL_ZIGBEE_Init */
  APP_ZIGBEE_TL_INIT();

  /* NVM Init */
#if CFG_NVM
  APP_ZIGBEE_NVM_Init();
#endif

  /* Register task */
  /* Create the different tasks */

  UTIL_SEQ_RegTask(1U << (uint32_t)CFG_TASK_NOTIFY_FROM_M0_TO_M4, UTIL_SEQ_RFU, APP_ZIGBEE_ProcessNotifyM0ToM4);
  UTIL_SEQ_RegTask(1U << (uint32_t)CFG_TASK_REQUEST_FROM_M0_TO_M4, UTIL_SEQ_RFU, APP_ZIGBEE_ProcessRequestM0ToM4);

  /* Task associated with network creation process */
  UTIL_SEQ_RegTask(1U << CFG_TASK_ZIGBEE_NETWORK_FORM, UTIL_SEQ_RFU, APP_ZIGBEE_NwkForm);


  /* Start the Zigbee on the CPU2 side */
  ZigbeeInitStatus = SHCI_C2_ZIGBEE_Init();
  /* Prevent unused argument(s) compilation warning */
  UNUSED(ZigbeeInitStatus);

  /* Initialize Zigbee stack layers */
  APP_ZIGBEE_StackLayersInit();

} /* APP_ZIGBEE_Init */

/**
 * @brief  Initialize Zigbee stack layers
 * @param  None
 * @retval None
 */
static void APP_ZIGBEE_StackLayersInit(void)
{
  enum ZbStatusCodeT status;
  APP_DBG("APP_ZIGBEE_StackLayersInit");

  zigbee_app_info.zb = ZbInit(0U, NULL, NULL);
  assert(zigbee_app_info.zb != NULL);

  /* Create the endpoint and cluster(s) */
  APP_ZIGBEE_ConfigEndpoints();

  /* Configure the joining parameters */
  zigbee_app_info.join_status = (enum ZbStatusCodeT) 0x01; /* init to error status */
  zigbee_app_info.join_delay = HAL_GetTick(); /* now */
  zigbee_app_info.startupControl = ZbStartTypeJoin;
  /* STEP 1 - TRY to START FROM PERSISTENCE */
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

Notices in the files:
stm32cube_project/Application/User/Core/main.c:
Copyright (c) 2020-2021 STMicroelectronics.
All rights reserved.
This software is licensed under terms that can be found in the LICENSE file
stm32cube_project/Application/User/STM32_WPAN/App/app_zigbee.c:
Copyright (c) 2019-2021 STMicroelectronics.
